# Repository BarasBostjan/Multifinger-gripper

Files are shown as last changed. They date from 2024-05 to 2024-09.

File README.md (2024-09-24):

# Multi-fingered gripper

Low-cost open-source 3D-printed reconfigurable multi-fingered gripper. Central to the design is the robotic finger module, which utilizes a single motor. A manual reconfigurable board supports multiple finger configurations, such as two-finger and three-finger setups.

## Under-actuated Finger
The design of the robotic finger was guided by two foundational requirements of our gripper. First, to maintain modularity, each finger was engineered to operate independently, both in terms of hardware and software. Second, in keeping with the objective to minimize costs, our design strategy focused on reducing the number of actuators used. Therefore, we aimed for a configuration with a single motor per finger. This led us to choose an under-actuated design for the fingers. Under-actuation allows for reduced costs while still enabling effective grasping and manipulation capabilities.

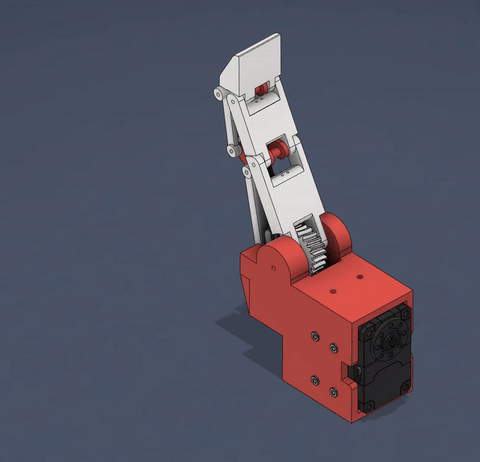
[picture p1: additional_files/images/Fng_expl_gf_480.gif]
Exploiding view of the finger design


## Reconfigurable Gripper
Our gripper is designed to enable manual reconfiguration. Although multi-fingered grippers with active reconfiguration offer faster and automatic adaptability, they are often not appropriate due to high costs and limited reconfiguration options. To merge versatility with cost-effectiveness, our design incorporates a manual reconfiguration mechanism.

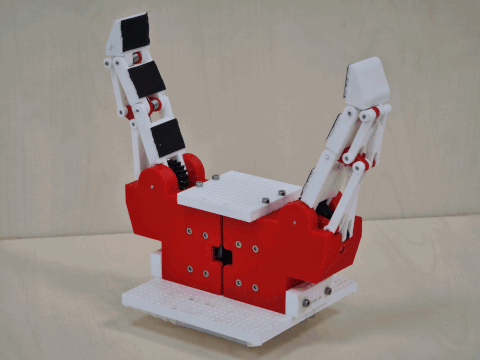
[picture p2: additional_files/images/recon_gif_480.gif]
Three examples of a gripper configuration


## Repository Description

This repository contains 3D models and guides for printing these models, including recommended materials and printer settings. It also includes a detailed list of required hardware and tools, step-by-step instructions for assembly. A control software written in Matlab along with a user manual is included.

### 3D Models and Printing Guides

Detailed descriptions of each 3D model available in this project and instructions for printing, including:
- Recommended materials
- Printer settings

### Assembly Instructions w/ the Bill of Materials

A complete list of all necessary materials, tools, and components required to build and run the project. This includes hardware components, motors, and other accessories. Step-by-step guide on how to assemble the components of the project.

### Software and Control

This project uses Matlab for control and automation. Included in this repository are:
- Source code for the control programs
- Manual explaining how to set up and use the software with the hardware

## Getting Started

1. Print the parts -> [3D Models and Printing Guide](3D%20models/)
2. Assemble the finger(s) -> [Assembly Instructions](assembly/)
3. Run the Matlab code -> [Software and Control](SW/)

## License

This work is licensed under the **Creative Commons Attribution-NonCommercial 4.0 International (CC BY-NC 4.0)**.  
For more details, please visit: [CC BY-NC 4.0 License](https://creativecommons.org/licenses/by-nc/4.0/).

## Citation

A citation for the associated paper will be added here once it is published.

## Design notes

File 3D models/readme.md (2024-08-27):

# Printing guide

Here we outline the entire process of printing the gripper. The following sections detail the printers used, materials, and challenges encountered during the printing process.

## 3D Printers

To realize digital 3D models, we used the Ultimaker S5 printer, which uses 2.85 mm diameter materials and operates with FFF (Fused Filament Fabrication) technology. This printer supports a wide range of materials (PLA, ABS, nylon, PVA, support, etc.) and can print with two different materials simultaneously. As the gripper parts sometimes have complex shapes and many holes for screws and pins, it is optimal to print the parts from one material and the supports from another. This allows for high-quality complex shapes and easy removal of supports.

For parts requiring greater precision, we used the Stratasys Objet 24 printer. This printer uses a photopolymer material, which is applied in layers and then cured with ultraviolet light. Due to the high cost of these materials, this printer is used less frequently and for smaller, high-precision parts (such as gears).

## Materials Used

The most frequently used material was PLA (polylactic acid) because it is the easiest to print with, due to its low melting point and glass transition temperature. However, PLA is not resistant to temperatures above approximately 60°C, as it becomes rubbery above its glass transition temperature of 55°C to 65°C.

When higher temperature resistance was needed, we used ABS (Acrylonitrile Butadiene Styrene) plastic. The glass transition temperature of ABS is between 105°C and 115°C, making it solid under our application conditions. ABS is harder to print than PLA because it requires higher nozzle, bed, and chamber temperatures and often more support structures during printing.

We found that PLA plastic was more suitable for creating finger joints and mechanical guides, while ABS plastic was better suited for creating the frame. When joints and guides were printed from ABS, these parts often cracked during assembly, forcing us to reprint them. Even if a part didn’t crack during the initial creation, it might crack when we attempted to modify the finger later. We did not encounter these issues with PLA, so all mechanical guides and finger joints in the final version were made from this material. The frame needed to be made from ABS since the motors heat up during operation.

The most challenging is the printing of the worm gear. Initially, both the worm and the gear were printed from Vera White plastic. Early tests involving motor-driven movement of the robotic finger revealed that the gear cracked under minor torques. We then printed the gear from PLA plastic. Initially, we thought these gears would be much more durable than the previous ones. However, durability tests of the finger showed that the PLA gears wore out quickly during rapid, repetitive gripping and releasing actions.

Ultimately, we printed the gears from nylon. With nylon gears, we did not observe the wear that was present with Vera White and PLA plastics. However, when the gears were made from nylon, the worm began to disintegrate. We have not yet addressed this issue, but it serves as a good starting point for further development of the robotic finger.

The reconfiguration board, top plates, auxiliary part and auxiliary attachments were all printed using PLA plastic.

As a support material, we commonly used Ultimaker Breakaway, which is easy to print and remove but can be challenging if located in inaccessible areas of the object. When removal of supports was predicted to be too difficult, we used BVOH (Butene Diol Vinyl Alcohol), a water-soluble material, making post-processing easier by dissolving supports in water.

## Possible Printing Challenges

#### Fit and Finish
Printed elements do not fit together correctly immediately after printing. -> Account for printer tolerances in the 3D models.

#### Support Material Issues
Support materials do not adhere well to the bed, requiring multiple print starts. -> This can be partially mitigated by using a brim around the model to ensure better adhesion.

#### Orientation of Prints
Cracks appear around the drilled holes. -> The orientation of printed elements affected their strength, particularly for ABS and PLA. Avoid drilling holes in the direction of the layers due to the weaker bonds between layers.

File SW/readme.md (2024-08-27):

# SW instructions for gripper control

This document provides instructions for using a MATLAB program designed to control a robotic gripper system, specifically with DYNAMIXEL XL430-W250 motors. It covers the necessary steps for hardware preparation, software configuration, and usage of the program’s core functions. By following these instructions, you can ensure the precise and reliable operation of the gripper system.

## Table of Contents
1. [Preparation](#preparation)
   1. [Setting Motor IDs](#setting-motor-ids)
   2. [Connecting Motors](#connecting-motors)
2. [MATLAB Program Overview](#matlab-program-overview)
3. [Basic Settings](#basic-settings)
4. [Calibration](#calibration)
   1. [When and Why to Calibrate?](#when-and-why-to-calibrate)
   2. [How to Calibrate?](#how-to-calibrate)
   3. [Calibration Parameters](#calibration-parameters)
   4. [Manipulating Calibration Parameters](#manipulating-calibration-parameters)
5. [Moving the Gripper Fingers](#moving-the-gripper-fingers)
   1. [Moving a Single Finger](#moving-a-single-finger)
   2. [Moving Multiple Fingers Simultaneously](#moving-multiple-fingers-simultaneously)
6. [Grasping](#grasping)
   1. [Grasping with a Single Finger](#grasping-with-a-single-finger)
   2. [Grasping with Multiple Fingers Simultaneously](#grasping-with-multiple-fingers-simultaneously)
   3. [Practical Tips for Grasping Functions](#practical-tips-for-grasping-functions)
7. [Other Functions](#other-functions)
   1. [Querying the Current Motor Rotation](#querying-the-current-motor-rotation)
   2. [Querying the Current Motor Torque](#querying-the-current-motor-torque)

## Preparation

### Setting Motor IDs

Before running the MATLAB code, it is necessary to set the IDs (addresses/sequence numbers) for the gripper motors. Each motor must be individually connected to the controller and the power supply. The motor has two connectors, allowing the first connector to be connected to the controller via a cable and the second to the power supply, regardless of which is the first or second connector on the motor. Then, launch the Dynamixel program `DYNAMIXEL Wizard 2` to set the motor IDs. The MATLAB program assumes the motor IDs are 1, 2, and 3, so these IDs must be set in the Dynamixel program. If multiple motors with the same ID are connected to the `DYNAMIXEL Wizard 2`, the program will not recognize them.

### Connecting Motors

Next, all gripper motors must be correctly connected. The motors are connected in series (the cable from the previous motor connects to the first connector of the next motor, and the second connector of the next motor connects to the following motor). The first motor in the series is connected to the controller, and the last to the power supply. This concludes the preparation.

## MATLAB Program Overview

The program was written using MATLAB version `R2022b` and is seperated into the folowing parts:

- `GripperControl.m` which is the main program for gripper control.

-  `functions_lib` is a library that contains all the necesary functions that are used in `GripperControl.m`

The `GripperControl.m` program operates as follows:
- Between lines 1 and 30, the program loads the necessary libraries, stores the addresses used by the motors, and prepares to connect the motors to MATLAB. These addresses are only valid for DYNAMIXEL XL430-W250 motors and should not be changed for the program to function correctly.
  
- Between lines 31 and 70, the program establishes a connection between MATLAB and the motors.
  
- In the following 20 lines, the basic motor settings are configured, including setting the motor operation mode and the maximum rotation speed. Calibration parameters and the default rotation speed are also set here.
  
- By line 103, the motors are turned on, and the program displays any connection errors.
  
- The main part of the program, marked with the comment "Main," contains the commands or functions that control the gripper.
  
- After the main section, the motors are turned off, and the connection between the motors and MATLAB is terminated.

## Basic Settings

It is possible to change the operating mode and maximum rotation speed of individual motors. Since the program's functions rely on these settings, it is advisable to leave them as they are. The `offset` and `max` lists can be set after all fingers have been calibrated to avoid recalibrating every time the program runs (except in the cases mentioned below). The last parameter that can be set here is `defaultSpeed`, which determines the speed at which the motors will rotate during movement and grasping functions if no specific speed is provided. The value ranges from 0 to 100, indicating the percentage of the motor's rotation speed, where 0 % means the motor is stationary, and 100 % represents the maximum rotation speed.

Parameter settings between lines 81 and 87 of the MATLAB program:

```matlab
global offset;
offset = [-7288 -16642 2943];

global max;
max = [23608 23608 23608];

global defaultSpeed;
defaultSpeed = 50;
```

## Calibration

### When and Why to Calibrate?

Calibration is required whenever the gripper is restarted or the gripper configuration is changed. Dynamixel XL430-250-T motors have absolute encoders for only one motor revolution. Multiple revolutions are measured incrementally, so the motor's rotation resets to a value within the first revolution (a number between 0 and 4095) each time it is powered off and on. Configuration changes can alter the working range of each finger. If calibration is not performed in the above scenarios, the finger may move out of its working range during program operation, potentially causing mechanical damage to the finger (e.g., gear breakage).

### How to Calibrate?

Calibration can be performed using the calibrate function. This function requires the motor ID for which calibration is desired. The function definition is as follows:

```matlab
calibrate(ID)
```

Calibration involves the motor closing the finger until it detects that the finger has reached the most closed angle for a given configuration. This is detected by measuring the motor torque, which increases beyond a certain threshold when the finger reaches the end angle. This angle is saved, then the motor reverses direction and similarly detects the other extreme angle of the finger, which is also saved. From the maximum and minimum angles, the function determines the global `offset` and `max` lists for the calibrated motor. Before calibrating, it is important to ensure that there is no object on the gripper, as the `calibrate` function expects the entire working range of the finger. The `offset` and `max` lists store motor calibration data. The `offset` list contains motor rotations at the most closed angle of the finger, while the `max` list contains data on the difference between the motor rotation at the most closed and most open angles of the finger.

The following MATLAB code demonstrates gripper calibration using the calibrate function:

```matlab
calibrate(1)
calibrate(2)
calibrate(3)
```

### Calibration Parameters

The `offset` and `max` lists store motor calibration data. The `offset` list contains motor rotations at the most closed position of the finger, while the `max` list contains data on the difference between the motor rotation at the most closed and most open positions of the finger.

These lists can be defined in the basic settings (see [Basic Settings](#basic-settings)). Calibration can be performed once, and the calibration parameters can then be entered into the basic settings. If the program is run multiple times, the fingers do not need to be recalibrated (unless the motors have been powered off or the gripper configuration has changed).

### Manipulating Calibration Parameters

It is often desirable for all fingers to have the same extreme positions. Some configurations result in fingers being calibrated to very similar extreme positions, while others may result in significantly different positions. To address this issue, the functions `calculateEqualMinimalMax` or `calculateEqualMax` can be used.

- The function `calculateEqualMinimalMax` does not take any input variables and does not return any values. When called, it modifies the `offset` and `max` lists to set the difference between the maximum and minimum positions of all fingers to the smallest difference between the maximum and minimum positions of any finger from the previous calibration. If executed correctly, the `max` list should contain identical values. After executing this function, the fingers will still have the same positions when fully open, but only the most closed positions of the fingers will change. This function is usually called immediately after finger calibration:

```matlab
calibrate(1)
calibrate(2)
calibrate(3)
calculateEqualMinimalMax()
```

- The function `calculateEqualMax` accepts one input variable, determining the difference between the maximum and minimum positions of all fingers. This function modifies the `offset` and `max` lists accordingly. If executed correctly, the `max` list should contain identical values. The function does not return any values. After executing this function, the fingers will still have the same positions when fully open, but only the most closed positions of the fingers will change. This function is usually called immediately after finger calibration.

In the example below, the fingers are first calibrated, and then the most closed position of the fingers is set to a value of 20,000 (i.e., the motor can rotate up to 20,000 pulses):

```matlab
calibrate(1)
calibrate(2)
calibrate(3)
calculateEqualMax(20000)
```

## Moving the Gripper Fingers

### Moving a Single Finger

To move one of the fingers to a specific angle, use the `moveOne` function. This function accepts three input variables. The first determines the motor ID or finger number, the second specifies the final angle of the finger, and the third is optional and determines the speed of the finger's movement. The function is defined as follows:

```matlab
moveOne(ID, moveTo)
moveOne(ID, moveTo, speed)
```

- The ID is entered as the number 1, 2, or 3.
  
- The final angles are recorded as a number between 0 and 100, representing the percentage of the finger's closure, where 0 % is a fully open finger and 100 % is a fully closed finger.
  
- If the third input variable is not entered, the function will determine the speed based on the global variable `defaultSpeed`, defined in the basic settings (see [Basic Settings](#basic-settings)).
  
- To control the finger's speed, enter the third input variable as a number between 0 and 100, representing the percentage of the motor's rotation speed, where 0 % is a stationary motor, and 100 % is the maximum rotation speed of the motor.

The following MATLAB code demonstrates the use of the `moveOne` function:

```matlab
moveOne(2, 50)
moveOne(1, 70, 100)
```

The first line closes finger number 2 to 50 %, with the speed determined by the basic settings. The second line closes finger number 1 to 70 % at 100 % speed.

### Moving Multiple Fingers Simultaneously

To move multiple fingers to specific angles simultaneously, use the `moveAll` function. This function can accept 1, 3, or 4 input variables and is defined as follows:

```matlab
moveAll(moveAllTo)
moveAll(move1To, move2To, move3To)
moveAll(move1To, move2To, move3To, speed)
```

- If only one input variable is entered into the function, it assumes that all three fingers should be moved to the same angles. As with the `moveOne` function, this value is entered as a number between 0 and 100, representing the percentage of the maximum angle. The fingers will move at a speed determined by the global variable `defaultSpeed`.

- If three input variables are entered into the function, each finger will be moved to its specified angle. From left to right, the variables represent the desired angles for fingers with IDs 1, 2, and 3. In this case, the function will respect the speed value recorded in the global variable `defaultSpeed` (see [Basic Settings](#basic-settings)). The function ensures that all fingers start and stop moving simultaneously. This means that if the fingers need to move different distances, the motor speeds will not be the same. The finger that needs to move the farthest will move at the default speed, while the other two fingers will move more slowly in proportion to the requirement for simultaneous movement.

- If four input variables are entered into the function, it will behave the same as when three variables are entered, except that in this case, the fourth variable determines the speed of the finger movement. The function will take the value entered in the fourth position, which must be recorded as a number between 0 and 100, representing the percentage of the maximum possible motor rotation speed. As with the three-variable case, only the finger that needs to move the farthest will move at the entered speed, while the other two fingers will move more slowly in proportion to the requirement for simultaneous movement.

The following MATLAB code demonstrates the use of the `moveAll` function:

```matlab
moveAll(30)
moveAll(30, 50, 70)
moveAll(30, 50, 70, 80)
```
The first line of code closes all fingers to 30 %, with the speed determined by the basic settings. The second line of code closes the first finger to 30 %, the second finger to 50 %, and the third finger to 70 %, with the speed determined by the basic settings. The third line closes all fingers to the same angles as the previous line but at 80 % speed.

## Grasping

### Grasping with a Single Finger

To grip an object with only one finger, use the `grabOne` function. This function accepts three input variables and is defined as follows:

```matlab
grabOne(ID, torque)
grabOne(ID, torque, speed)
```

- The first variable determines the motor ID or finger number.
  
- The second determines the motor torque.
  
- The third is optional and determines the speed of the finger's movement.
  
- The ID is entered as the number 1, 2, or 3.
  
- The motor torque is recorded as a number between 0 and 100, representing the percentage of the maximum allowable motor torque, where 0 % means the motor exerts no torque and 100 % means the motor exerts the maximum allowable torque.
  
- If the third input variable is not entered, the function will determine the speed based on the global variable `defaultSpeed`, defined in the basic settings (see [Basic Settings](#basic-settings)).
  
- To control the finger's speed, enter the third input variable as a number between 0 and 100, representing the percentage of the motor's rotation speed, where 0 % is a stationary motor, and 100 % is the maximum rotation speed of the motor.

The function works by gradually closing the finger until the measured torque on the motor exceeds the desired torque. At that point, the motor stops, and the finger remains stationary.

The following MATLAB code demonstrates the use of the `grabOne` function:

```matlab
grabOne(2, 50)
grabOne(1, 70, 100)
```

The first line of code grasps with finger number 2 at 50 % torque, with the speed determined by the basic settings. The second line of code grasps with finger number 1 at 70 % torque and 100 % speed.

### Grasping with Multiple Fingers Simultaneously

To grip an object with multiple fingers simultaneously, use the `grabAll` function. This function can accept 1, 3, 4, or 6 input variables and is defined as follows:

```matlab
grabAll(torqueAll)
grabAll(torque1, torque2, torque3)
grabAll(torque1, torque2, torque3, speedAll)
grabAll(torque1, torque2, torque3, speed1, speed2, speed3)
```

- If only one input variable is entered into the function, it assumes that all fingers should grip with the same desired maximum torque on all motors. Enter the desired maximum torque value as the sole input variable. The value must be recorded as a number between 0 and 100, which, similar to the `grabOne` function, determines the maximum desired torque value as a percentage of the maximum allowable torque. The fingers will move at a speed determined by the global variable `defaultSpeed` (see [Basic Settings](#basic-settings)). The function begins closing all fingers simultaneously. When the measured torque on any finger exceeds the desired torque, that motor stops, and the finger remains stationary. This action does not affect the other fingers, which can continue moving until all fingers stop due to the conditions mentioned above. The function terminates when all fingers stop.

- If three input variables are entered into the function, it will behave the same as with one input variable, except that each motor will stop rotating at its specified maximum torque. From left to right, the three maximum desired torques for motors with IDs 1, 2, and 3 are specified. For each of the three variables, enter a value between 0 and 100, the same as in the previous case and similar to the `grabOne` function. The fingers will move at a speed determined by the global variable `defaultSpeed`.

- If four input variables are entered into the function, it will behave the same as with three input variables, except that now the fourth variable determines the speed of the finger movement. The function takes the value entered in the fourth position instead of the global variable `defaultSpeed`, which must be recorded as a number between 0 and 100, representing the percentage of the maximum possible motor rotation speed. In this case, all three fingers will move at the same entered speed.

- If six input variables are entered into the function, it will behave the same as with three input variables, except that now the last three variables determine the speeds of the fingers' movements. The function takes the values entered in the last three positions instead of the global variable `defaultSpeed`, arranged from left to right as the speeds for motors with IDs 1, 2, and 3. The values must be recorded as a number between 0 and 100, representing the percentage of the maximum possible motor rotation speed.

The following MATLAB code demonstrates the use of the `grabAll` function:

```matlab
grabAll(30)
grabAll(30, 50, 70)
grabAll(30, 50, 70, 80)
grabAll(30, 50, 70, 20, 60, 80)
```

The first line of code grasps with all fingers at 30 % torque, with the speed determined by the basic settings. The second line grasps with 30 % torque on the first finger, 50 % on the second finger, and 70 % on the third finger, with the speed determined by the basic settings. The third line grasps with the same torques as the previous line, but this time the fingers move at 80 % speed. The last line grasps with the same torque as the previous two lines, but now the first motor moves at 20 % speed, the second at 60 % speed, and the third at 80 % speed.

### Practical Tips for Grasping Functions

The `grabAll` function can also be used to move only 2 or just 1 motor. This is done by setting either the desired maximum torque or the speed of the finger that you want to remain stationary to 0. If possible, it is better to set the speed to 0 because in this case, the motor is not initialized, whereas if only the torque is set to 0, the motor will still attempt to move momentarily until it measures the minimum torque. Correct usage examples:

```matlab
grabAll(40, 50, 0, 80)
grabAll(40, 50, 50, 50, 50, 0)
```

In both of the above examples, we grip with the first two fingers while the third finger remains stationary. In the first line of MATLAB code, the third motor's torque is set to 0, while in the second line, the third motor's speed is set to 0.

When setting the desired maximum torque, ensure that it is not set too low. The motor exerts some torque even when it is just moving freely. A general rule of thumb is that this value should be set to at least 30 %, otherwise, the motor may stop immediately. At the upper end, nothing limits the user from setting the desired maximum torque above 100 %. The motors driving the fingers are strong enough to generate even more than 300% of the maximum allowable torque, but this would likely result in mechanical failure (e.g., the worm gear could break). 100 % was chosen in this MATLAB program based on experience with the fingers and represents a confident value at which the fingers should never be damaged. It is possible to go above 100 %, but there is no guarantee that the finger will remain undamaged.

## Other Functions

### Querying the Current Motor Rotation

To query the current rotation of a motor for one of the fingers, use the `readRotation` function. This function accepts one input variable that determines the motor ID and returns the current motor rotation value. The value returned by the function already accounts for calibration parameters, so the function would return a rotation of 0 in the most closed position of the finger and the value of the `max` list for the motor with the given ID in the most open position. For other finger positions, the value will fall somewhere between these two values. Example query for the current rotation of the second motor:

```matlab
currentRotation = readRotation(2)
```

### Querying the Current Motor Torque

To query the current torque value on a motor for one of the fingers, use the `readTorque` function. This function accepts one input variable that determines the motor ID and returns the current torque value on that motor. The function always returns a positive torque value, regardless of the direction of torque on the motor. Example query for the current torque on the second motor:

```matlab
currentTorque = readTorque(2)
```

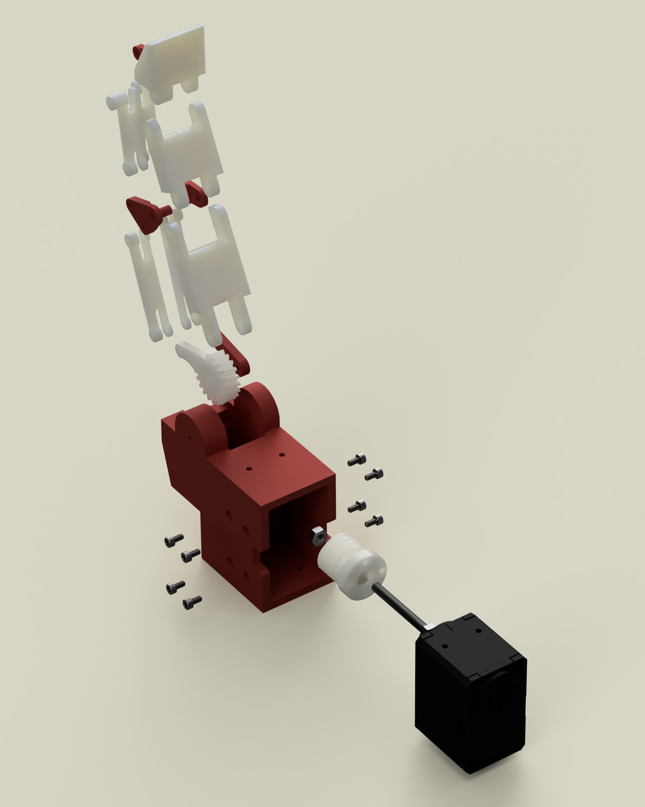
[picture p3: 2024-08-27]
additional_files/images/Exploding_view.PNG

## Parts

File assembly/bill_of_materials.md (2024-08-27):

| Part Name | Quantity | Material Name  |
|--- |:---:|---:|
| Frame | 1 | ABS |
| XL-430 | 1 | / |
| Worm gear adapter | 1 | PLA |
| Worm gear | 1 | PLA |
| Worm wheel | 1 | PLA |
| Distal phalanx | 1 | PLA |
| Intermediate phalanx | 1 | PLA |
| Proximal phalanx | 1 | PLA |
| Intermediate transition linkage left | 1 | PLA |
| Intermediate transition linkage right | 1 | PLA |
| Proximal transition linkage left | 1 | PLA |
| Proximal transition linkage right | 1 | PLA |
| Bottom torsion linkage | 1 | PLA |
| Central torsion linkage left | 1 | PLA |
| Central torsion linkage right | 1 | PLA |
| Upper torsion linkage | 1 | PLA |
| M2,5X5 Socket Head Screw (91290A100) | 8 | Steel |
| M4X25 Hex Head Screw (91280A144) | 1 | Steel |
| M2X5 Socket Head Screw (91290A012) | 4 | Steel |
| Rod 250 mm length 2mm diameter | 1 | Stainless Steel|
| Rubber pads | 3 | rubber |

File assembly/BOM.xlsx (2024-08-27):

Part Name | finger
Working BOM | as of June 16, 2024 at 10:18:56 AM UTC
Exported by | bb1625@student.uni-lj.si
Time of Export | 12:18 PM Jun 16, 2024
Level | Part Name | Quantity | Material Name
 | base | 1 | ABS
 | XL-430 | 1 | /
 | worm gear adapter | 1 | PLA
 | worm gear | 1 | PLA
 | gear with linkage | 1 | PLA
 | segment 1 | 1 | PLA
 | segment 2 | 1 | PLA
 | segment 3 | 1 | PLA
 | linkage 1 | 1 | PLA
 | linkage 2 | 1 | PLA
 | linkage 3 | 1 | PLA
 | linkage 4 | 1 | PLA
 | bottom linkage | 1 | PLA
 | central linkage 1 | 1 | PLA
 | central linkage 2 | 1 | PLA
 | upper linkage | 1 | PLA
 | 91290A100_Black-Oxide Alloy Steel Socket Head Screw | 8 | Steel
 | 91280A144_Medium-Strength Class 8.8 Steel Hex Head Screw | 1 | Steel
 | 91290A012_Black-Oxide, M2 x 0.4 mm Thread, 5 mm Long | 4 | Steel
 | rod 250 mm length 2mm diameter | 1 | Stainless Steel
 | rubber pads | 3 | rubber

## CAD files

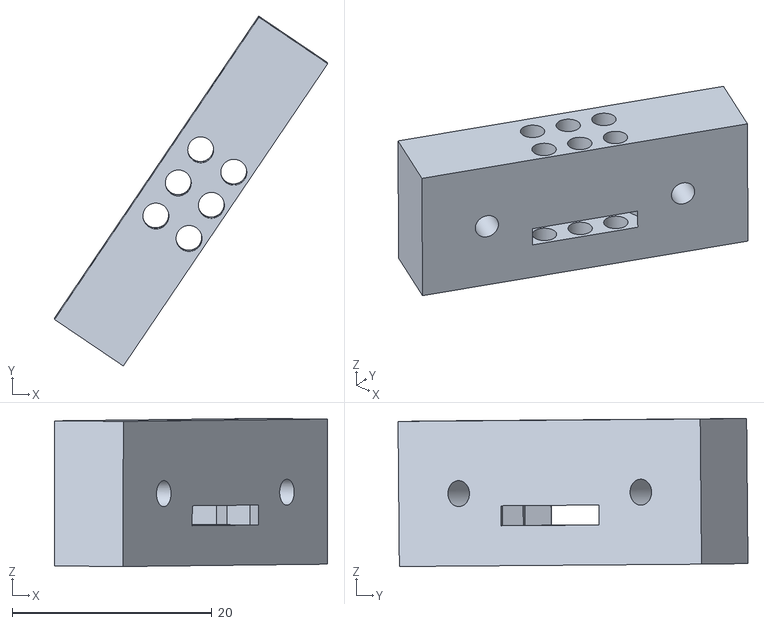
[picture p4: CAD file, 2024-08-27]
3D models/configuration parts/auxiliary attachment 1.stl
27.4 x 35.0 x 14.8

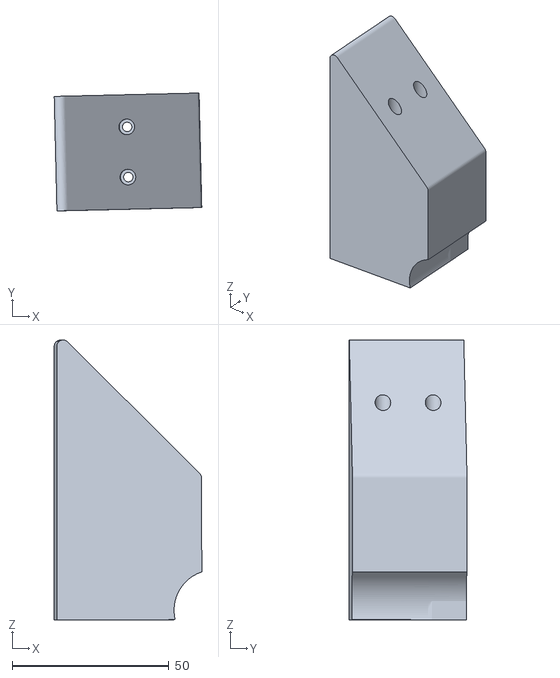
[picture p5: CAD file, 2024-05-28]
3D models/finger testers/tester 4.stl
47.0 x 37.6 x 89.2

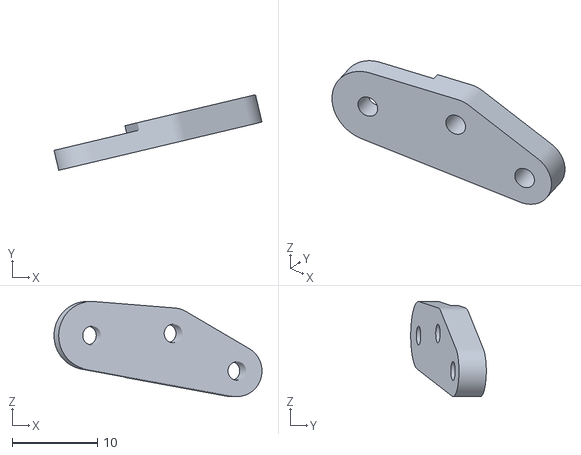
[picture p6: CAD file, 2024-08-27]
3D models/finger/central torsion linkage right.stl
24.4 x 8.87 x 11.2

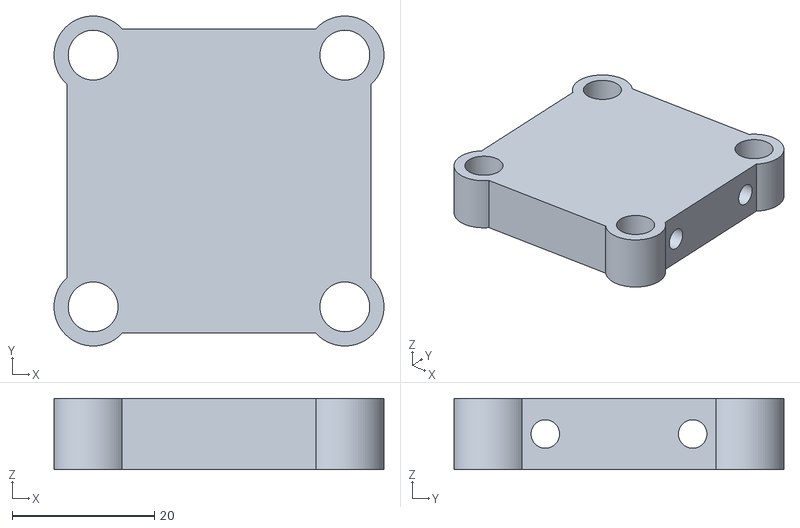
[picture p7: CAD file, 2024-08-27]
3D models/configuration parts/auxiliary part.stl
46.4 x 46.4 x 10.0

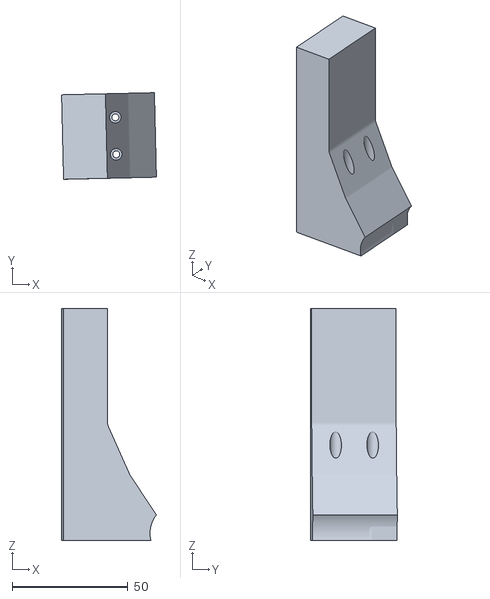
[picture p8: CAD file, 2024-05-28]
3D models/finger testers/tester 6.stl
41.0 x 37.4 x 100.2

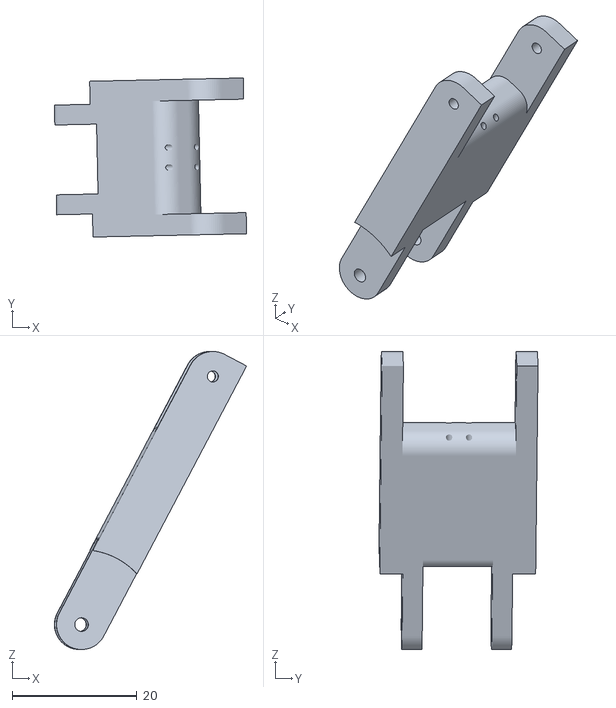
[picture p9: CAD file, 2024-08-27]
3D models/finger/proximal phalanx.stl
30.8 x 25.5 x 47.8

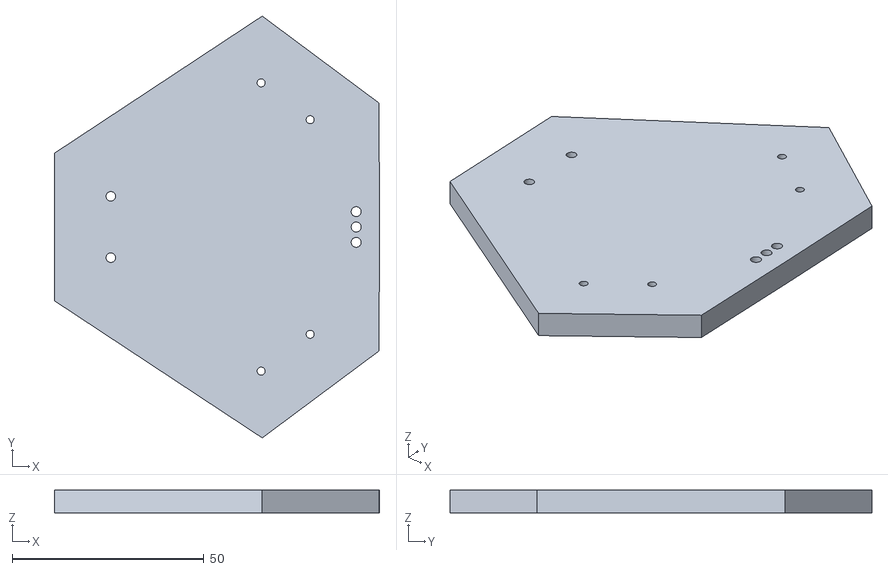
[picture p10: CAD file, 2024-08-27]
3D models/configuration parts/top plate for circular 3 finger gripper.stl
84.8 x 110.0 x 6.00

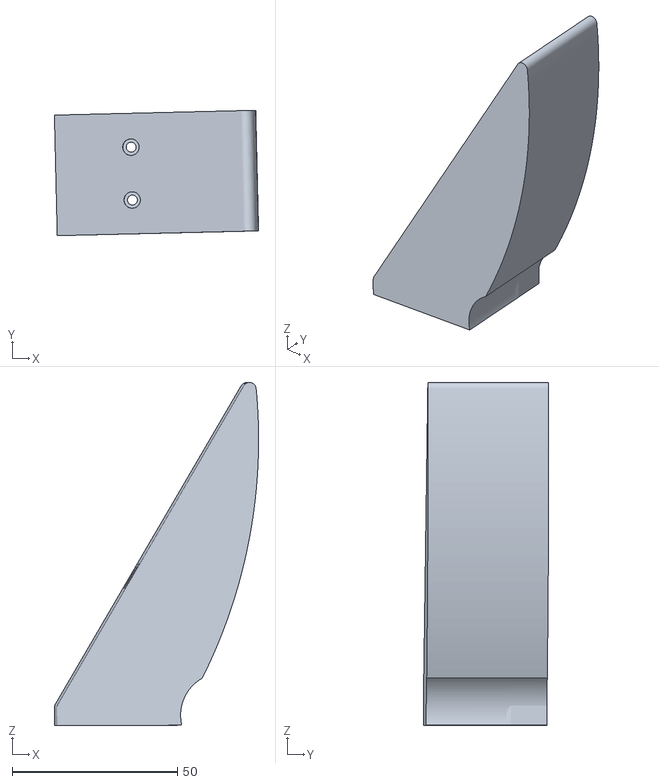
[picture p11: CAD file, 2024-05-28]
3D models/finger testers/tester 7.stl
61.8 x 37.9 x 103.8

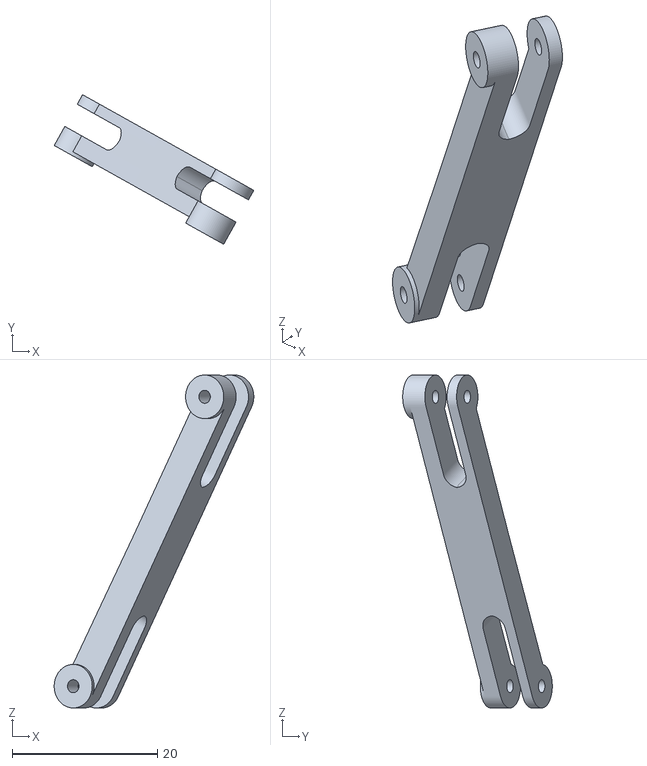
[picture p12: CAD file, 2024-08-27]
3D models/finger/proximal transition linkage right.stl
27.5 x 20.6 x 45.8

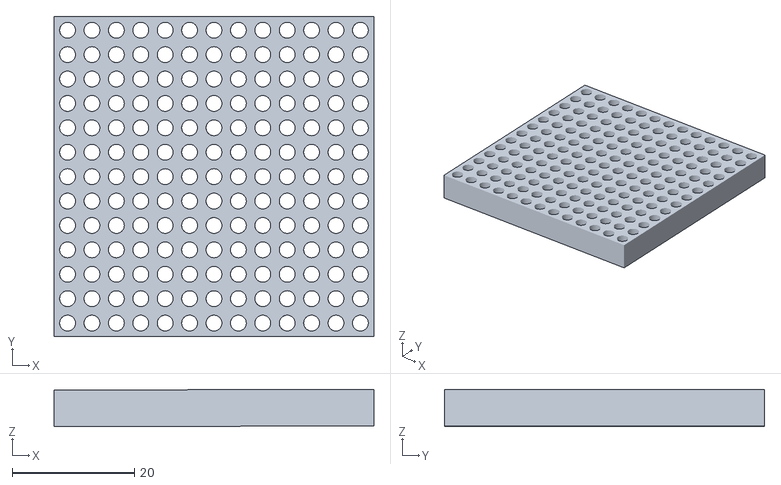
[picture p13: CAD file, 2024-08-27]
3D models/configuration parts/top plate for 2 finger gripper.stl
52.4 x 52.5 x 6.11

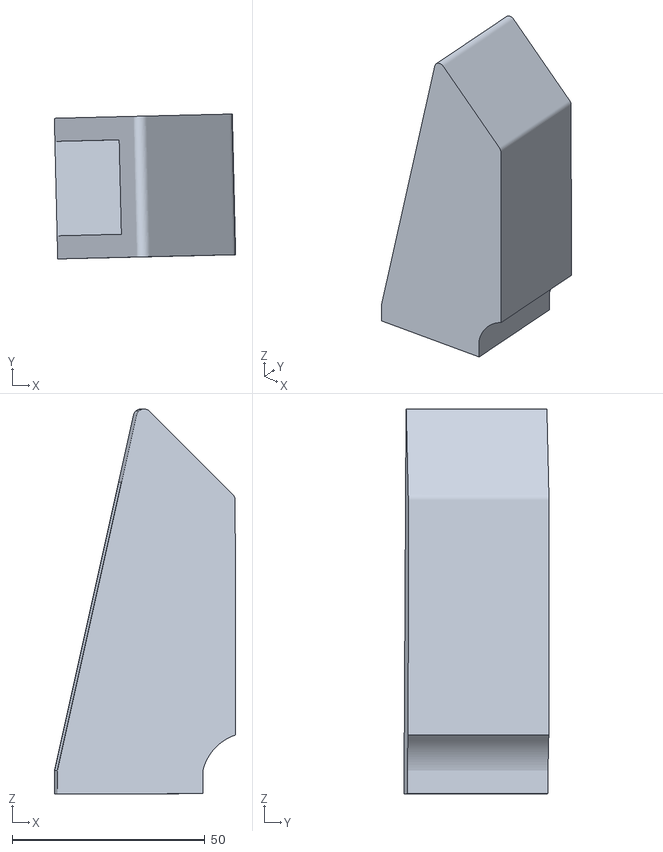
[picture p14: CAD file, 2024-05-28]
3D models/finger testers/tester 5.stl
47.0 x 37.6 x 99.9

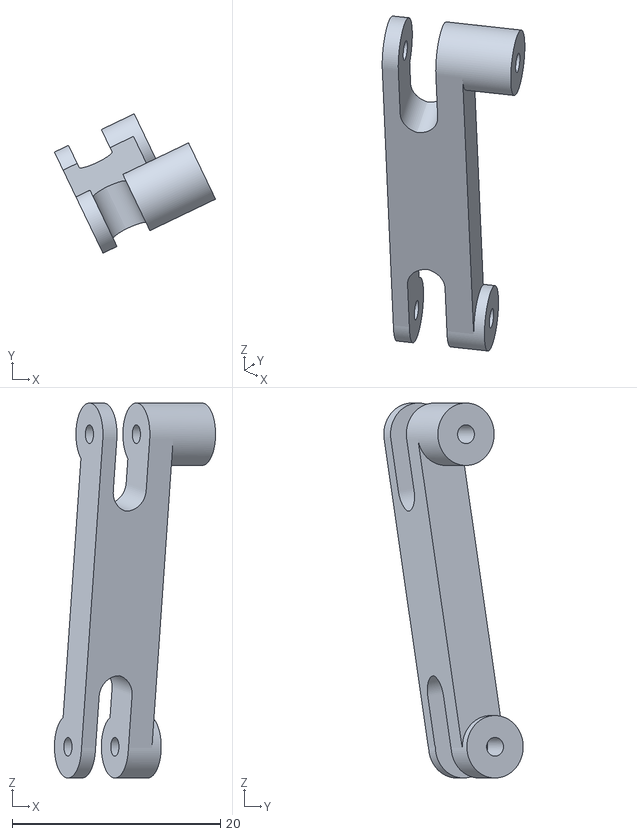
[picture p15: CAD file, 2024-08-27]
3D models/finger/intermediate transition linkage left.stl
15.5 x 13.4 x 36.0

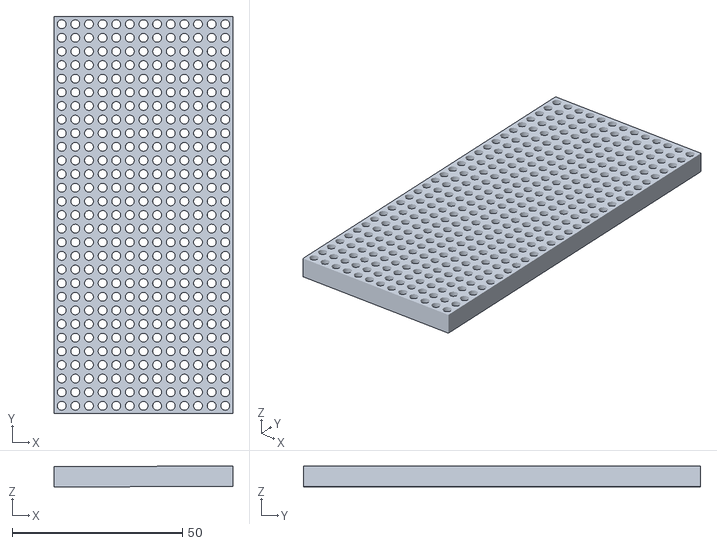
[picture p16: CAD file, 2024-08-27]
3D models/configuration parts/top plate for parallel 3 finger gripper.stl
52.4 x 116.5 x 6.11

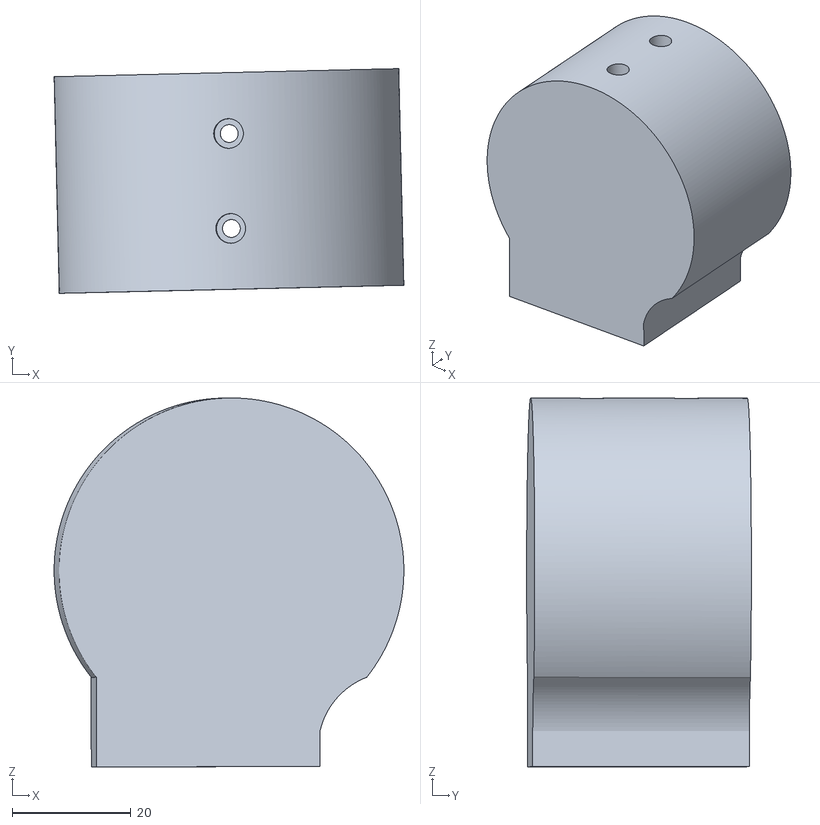
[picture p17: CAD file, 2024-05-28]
3D models/finger testers/tester 2.stl
58.9 x 37.9 x 62.2

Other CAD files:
3D models/finger/bottom torsion linkage.stl
3D models/configuration parts/auxiliary attachment 2.stl
3D models/finger testers/tester 1.stl
3D models/finger/upper torsion linkage.stl
3D models/configuration parts/handle.stl
3D models/finger testers/tester 3.stl
3D models/finger/central torsion linkage left.stl
3D models/finger/distal phalanx.stl
3D models/finger/frame.stl
3D models/finger/intermediate phalanx.stl
3D models/finger/intermediate transition linkage right.stl
3D models/finger/proximal transition linkage left.stl
3D models/finger/worm gear adapter.stl
3D models/finger/worm gear.stl
3D models/finger/worm wheel.stl

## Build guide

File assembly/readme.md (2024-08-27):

# Assembly Instructions

This section instructions for assembling the robotic fingers and gripper. Follow these steps carefully to ensure correct and efficient assembly of your robotic system.

## Assembly of the Fingers

<figure>
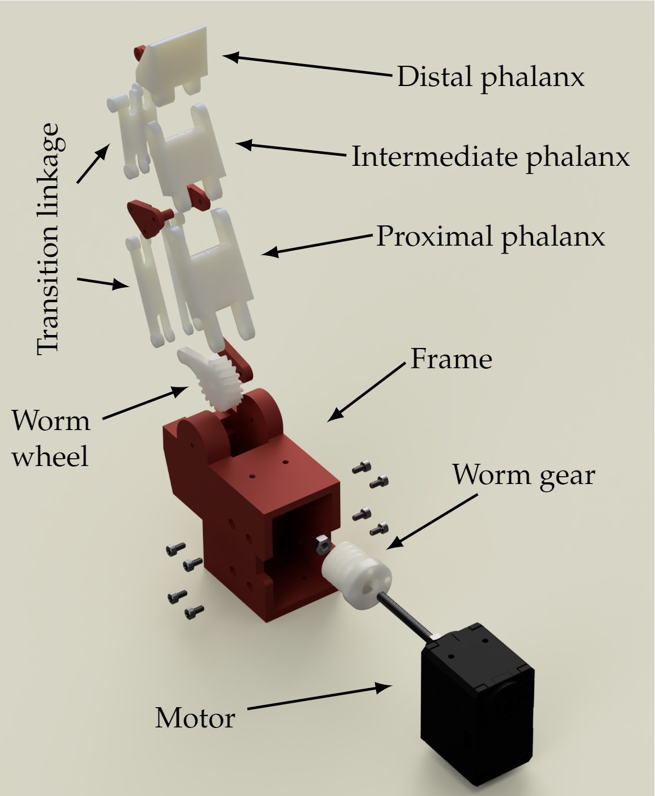
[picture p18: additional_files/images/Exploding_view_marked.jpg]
Exploiding view of the finger design

<figcaption> Exploding view of the finger with the main components marked.</figcaption>
</figure>

### 1. Print Components
Begin by 3D printing all parts of the robotic finger (see [3D Models and Printing Guide](3D_models/)).
### 2. Assemble Joints
Connect the printed elements that form each joint using 2 mm diameter stainless steel rods. Cut the rods to the appropriate lengths, align the elements, and insert the rods through them.
### 3. Install Torsion Springs
During the joint assembly, incorporate torsion springs. Insert each end of the torsion spring into pre-designed holes in the elements. These springs are essential as they help the finger return to a fully extended position when not in use.

<figure>
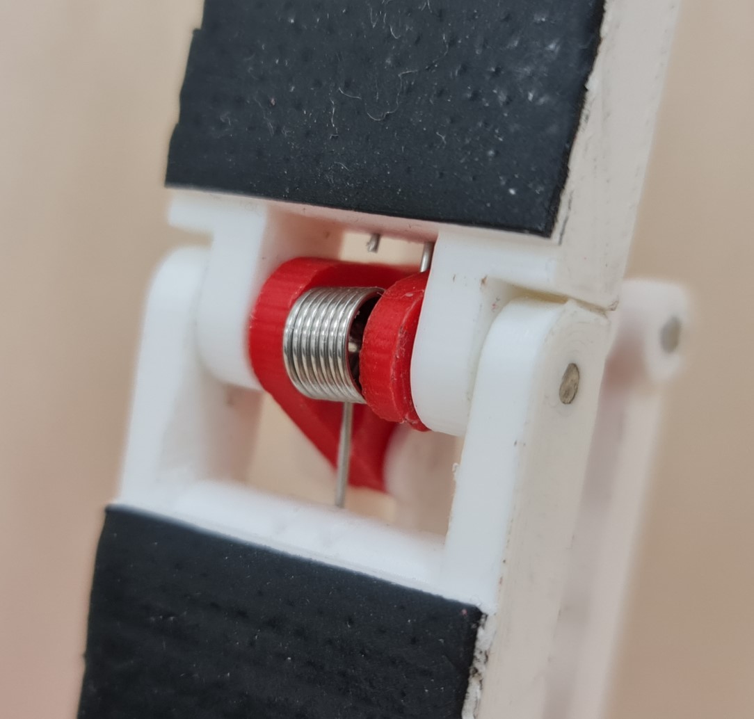
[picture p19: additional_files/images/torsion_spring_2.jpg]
Torsion spring.

<figcaption> Torsion spring installed at the joint.</figcaption>
</figure>

### 4. Attach to Frame
Secure the assembled finger to the frame with a metal rod to form the main joint.
### 5. Motor and Worm Installation
Attach the worm gear to the motor with four screws. Subsequently, place the motor with the attached worm into the frame and secure it using eight M2 screws, each 6 mm in length.
### 6. Enhance Grip Strength
Apply a strip of self-adhesive rubber to each joint of the robotic finger to improve the grip strength.

## Assembly of the Gripper

<figure>
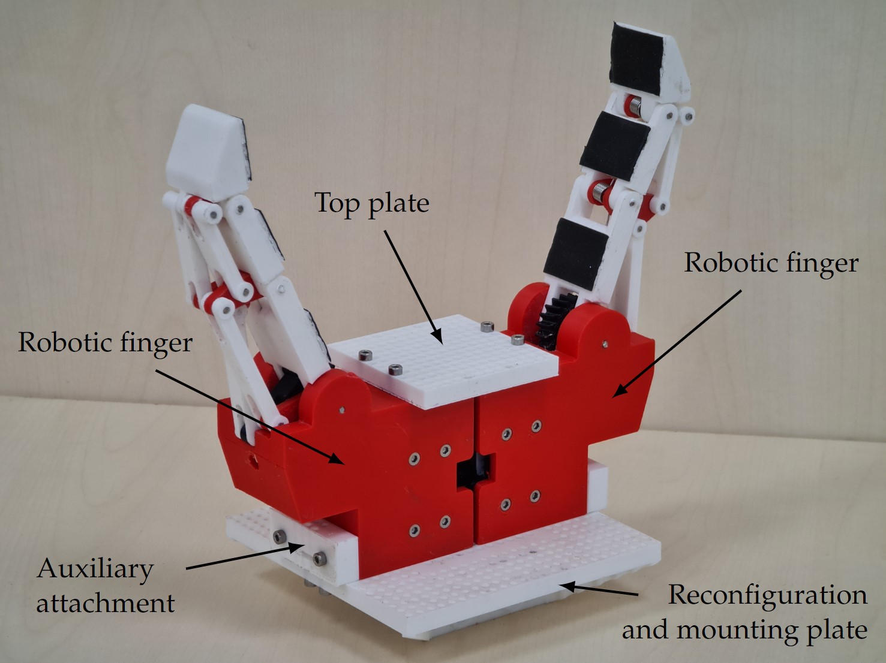
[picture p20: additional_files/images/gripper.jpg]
An example two-finger gripper configuration with all the parts of the reconfiguration mechanism marked

<figcaption> An example configuration with all the parts of the reconfiguration mechanism marked.</figcaption>
</figure>

### 1. Layout Planning
Determine how to arrange the robotic fingers on the distribution plate using 3D models for guidance. Ensure that the selected holes for mounting are not obstructed by the plate’s attachment system to the robotic arm.
### 2. Choose Base and Support Elements
Select an appropriate base for the fingers and any necessary auxiliary support elements.
### 3. Position Fingers
Adjust each robotic finger to its most open state to ensure unobstructed access to the screw openings.
### 4. Wire Motors
Before mounting, connect the motors with wires. Properly organizing the wires at this stage helps to avoid access issues later.
### 5. Mount the Fingers
Securely position and fasten the robotic fingers to the designated spots on the plate using 6 mm Allen bolts.
### 6. Install Auxiliary Elements
If additional support elements are needed for your configuration, attach them at this point.
### 7. Secure the Base 
Finally, place the base over the fingers. From above, attach the base to the robotic fingers and any auxiliary elements using screws.

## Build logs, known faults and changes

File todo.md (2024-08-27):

# Things to do before submission MD:
- Move files to new folders / delete old ones
- ~~Write instructions for assembly~~
- Write SW instructions
# Next steps for BB:
- Rename all files to use english!
- Add all *needed* models to 3D_models folder (use subfolders)
- Write/add bill of materials in assembly
- Add SW to SW folder (use subfolders)

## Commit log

2024-05-28 Rename tester 2 updated.stl to tester 2.stl
    [tester 2.stl]
2024-05-28 Rename tester 3 updated.stl to tester 3.stl
    [tester 3.stl]
2024-05-28 Rename tester 4 updated.stl to tester 4.stl
    [tester 4.stl]
2024-05-28 Rename tester 6 updated.stl to tester 6.stl
    [tester 6.stl]
2024-05-28 Rename tester 7 updated.stl to tester 7.stl
    [tester 7.stl]
2024-06-05 Create 3D Models and Printing Guide.md
2024-06-05 Create Assembly Instructions.md
2024-06-16 Rename clen 1.stl to segment 1.stl
    [segment 1.stl]
2024-06-16 Rename clen 2.stl to segment 2.stl
    [segment 2.stl]
2024-06-16 Rename clen 3.stl to segment 3.stl
    [segment 3.stl]
2024-06-16 Rename usmernik 1.stl to linkage 1.stl
    [linkage 1.stl]
2024-06-16 Rename usmernik 2.stl to linkage 2.stl
    [linkage 2.stl]
2024-06-16 Rename usmernik 3.stl to linkage 3.stl
    [linkage 3.stl]
2024-06-16 Rename usmernik 4.stl to linkage 4.stl
    [linkage 4.stl]
2024-06-16 Rename vodilo na sredini 2.stl to central linkage 2.stl
    [central linkage 2.stl]
2024-06-16 Rename vodilo na sredini.stl to central linkage.stl
    [central linkage.stl]
2024-06-16 Rename central linkage.stl to central linkage 1.stl
    [central linkage 1.stl]
2024-06-16 Rename vodilo spodaj.stl to bottom linkage.stl
    [bottom linkage.stl]
2024-06-16 Rename vodilo za prst.stl to upper linkage.stl
    [upper linkage.stl]
2024-06-16 Rename zobnik.stl to gear with linkage.stl
    [gear with linkage.stl]
2024-06-16 Update and rename plate.stl to board.stl
    [board.stl]
2024-07-08 Rename central linkage 1.stl to central torsion linkage right.stl
    [central torsion linkage right.stl]
2024-07-08 Rename central linkage 2.stl to central torsion linkage left.stl
    [central torsion linkage left.stl]
2024-07-08 Rename bottom linkage.stl to bottom torsion linkage.stl
    [bottom torsion linkage.stl]
2024-07-08 Rename gear with linkage.stl to worm wheel.stl
    [worm wheel.stl]
2024-07-08 Rename linkage 2.stl to proximal transition linkage right.stl
    [proximal transition linkage right.stl]
2024-07-08 Rename linkage 1.stl to proximal transition linkage left.stl
    [proximal transition linkage left.stl]
2024-07-08 Update GripperControl.m
    slovenski komentarji so spremenjeni v angleške
